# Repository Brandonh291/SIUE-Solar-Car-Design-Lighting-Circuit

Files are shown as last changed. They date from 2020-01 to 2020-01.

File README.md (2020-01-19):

# SIUE-Solar-Car-Design-Lighting-Circuit
Solar Car Lighting Circuit
Lighting Controller MCU specifications

Read through section 9.4 of the 2020 regulations for how the external lights should behave.

Also, download the orion bms wiring sheet, it’ll be useful.

· The lighting controller will dictate when a light on the car turns on and off

· It will control 10 exterior lights

o Two forward facing headlights

o Two forward facing blinkers

o Two lateral blinkers

o Three rear lights, two of which are blinker/break and one of which is a break light

o One BPS trip strobe

· The behavior of the lights is as follows:

o The headlights will be controlled by a toggle switch. When the switch is closed, the headlights will turn on. When the switch is opened the headlights will turn off.

o The blinkers will be controlled by a three-state toggle switch. When the switch is turned left, the forward, lateral, and rear left lights will begin blinking. The same for if the switch is turned right. If the switch is neutral, no blinking will occur.

o The brakes will illuminate when the brake petal is depressed. Two of the three brake lights in the rear of the vehicle will also function as blinkers. When the blinkers and brakes are engaged, the blinkers take priority.

o The hazard will be controlled by a toggle switch. When it is closed, all lights except for the BPS strobe will flash until the switch is opened.

o The BPS strobe is controlled by an open drain output from the Orion BMS. Normal, working conditions will set the output high. When the device detects a battery fault, the output goes low. See the “Digital Signal outputs” section in the Orion BMS wiring manual for more information.

· Power requirements

o Each LED strip burns about 50mA at 12V, so whatever is used to switch them must be capable of handling this load. In the case of the headlights, and each front/lateral set of blinkers, are tied together, so the switch powering them must be able to handle approximately 100mA. There are logic level FETs that can drive the LEDs.

o I want input protection on the switches to make it ESD resistant. A google search for “MCU input protection” will yield plenty of results.

· Hardware and I/O

o It’d be nice if the I/O was confined to a single connector like a D-sub connector or something similar to confine all the connections to a single plug.

Parts List
  * 14 - 3.5mm 2 Pin Screw Terminal Block
  * 7 - 10k Resistors
  * 7 - 2k Resistors
  * 1 - 1M Resistor
  * 1 - Arduino Nano Microcontroller
  * 7 - RFP30N06LE Mosfets
  * 2 - 74HC08N Quad 2 Input AND IC
  * 1 - 74LS04N Hex Inverter IC
  * 1 - 74HC32N Quad 2 Input OR IC
  * 1 - NE555N Timer
  * 1 - 470nF Capacitor
  * 1 - 10nF Capacitor

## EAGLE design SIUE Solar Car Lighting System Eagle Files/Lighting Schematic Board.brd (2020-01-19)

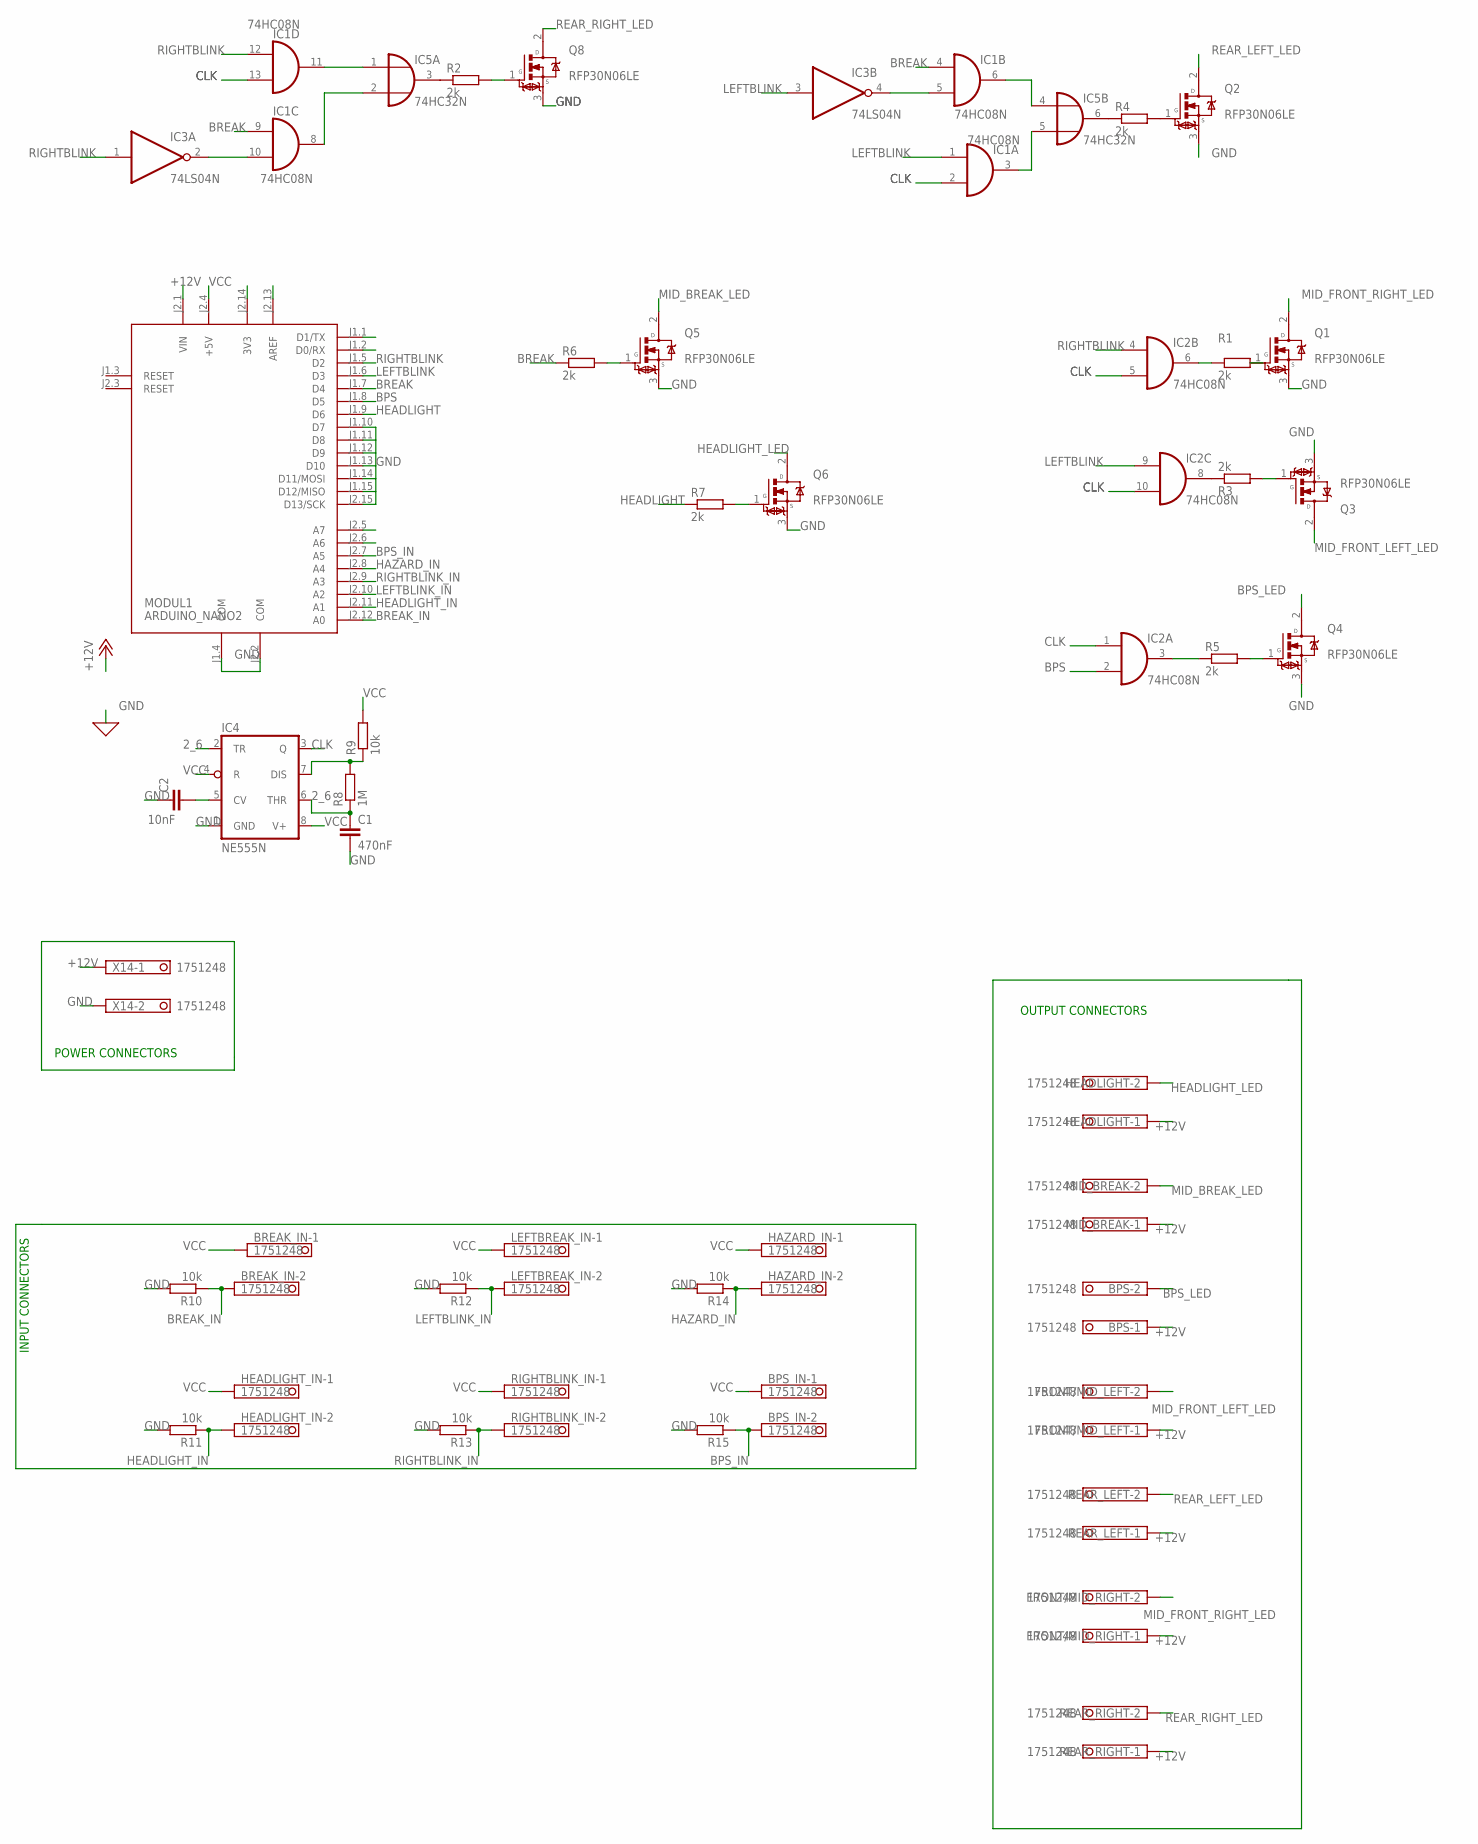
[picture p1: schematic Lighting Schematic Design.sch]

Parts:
BPS: 1751248
BPS_IN: 1751248
BREAK_IN: 1751248
C1: 470nF; C2.5-2
C2: 10nF; C2.5-2
FRONT/MID_LEFT: 1751248
FRONT/MID_RIGHT: 1751248
HAZARD_IN: 1751248
HEADLIGHT: 1751248
HEADLIGHT_IN: 1751248
IC1, IC2: 74HC08N; DIL14
IC3: 74LS04N; DIL14
IC4: NE555N; DIL08
IC5: 74HC32N; DIL14
LEFTBREAK_IN: 1751248
MID_BREAK: 1751248
MODUL1: ARDUINO_NANO2
Q1, Q2, Q3, Q4, Q5, Q6, Q8: RFP30N06LE; TRANS_RFP30N06LE
R1, R2, R3, R4, R5, R6, R7: 2k; 0204/5
R8: 1M; 0204/5
R9, R10, R11, R12, R13, R14, R15: 10k; 0204/5
REAR_LEFT: 1751248
REAR_RIGHT: 1751248
RIGHTBLINK_IN: 1751248
X14: 1751248

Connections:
2_6: C1.1, IC4.2 (TR), IC4.6 (THR), R8.1
+12V: BPS.1, FRONT/MID_LEFT.1, FRONT/MID_RIGHT.1, HEADLIGHT.1, MID_BREAK.1, MODUL1.J2.1 (VIN), REAR_LEFT.1, REAR_RIGHT.1, X14.1
BPS: IC2.2 (I1), MODUL1.J1.8 (D5)
BPS_IN: BPS_IN.2, MODUL1.J2.7 (A5), R15.1
BPS_LED: BPS.2, Q4.2 (D)
BREAK: IC1.4 (I0), IC1.9 (I0), MODUL1.J1.7 (D4), R6.1
BREAK_IN: BREAK_IN.2, MODUL1.J2.12 (A0), R10.1
CLK: IC1.2 (I1), IC1.13 (I1), IC2.1 (I0), IC2.5 (I1), IC2.10 (I1), IC4.3 (Q)
GND: C1.2, C2.1, IC1.7 (GND), IC2.7 (GND), IC3.7 (GND), IC4.1 (GND), IC5.7 (GND), MODUL1.J1.4 (COM), MODUL1.J1.10 (D7), MODUL1.J2.2 (COM), MODUL1.J2.15 (D13/SCK), Q1.3 (S), Q2.3 (S), Q3.3 (S), Q4.3 (S), Q5.3 (S), Q6.3 (S), Q8.3 (S), R10.2, R11.2, R12.2, R13.2, R14.2, R15.2, X14.2
HAZARD_IN: HAZARD_IN.2, MODUL1.J2.8 (A4), R14.1
HEADLIGHT: MODUL1.J1.9 (D6), R7.1
HEADLIGHT_IN: HEADLIGHT_IN.2, MODUL1.J2.11 (A1), R11.1
HEADLIGHT_LED: HEADLIGHT.2, Q6.2 (D)
LEFTBLINK: IC1.1 (I0), IC2.9 (I0), IC3.3 (I), MODUL1.J1.6 (D3)
LEFTBLINK_IN: LEFTBREAK_IN.2, MODUL1.J2.10 (A2), R12.1
MID_BREAK_LED: MID_BREAK.2, Q5.2 (D)
MID_FRONT_LEFT_LED: FRONT/MID_LEFT.2, Q3.2 (D)
MID_FRONT_RIGHT_LED: FRONT/MID_RIGHT.2, Q1.2 (D)
unnamed: Q8.1 (G), R2.2
unnamed: IC1.10 (I1), IC3.2 (O)
unnamed: IC2.6 (O), R1.1
unnamed: IC1.5 (I1), IC3.4 (O)
unnamed: IC4.7 (DIS), R8.2, R9.1
unnamed: Q2.1 (G), R4.2
unnamed: Q1.1 (G), R1.2
unnamed: Q3.1 (G), R3.2
unnamed: Q4.1 (G), R5.2
unnamed: IC2.3 (O), R5.1
unnamed: Q5.1 (G), R6.2
unnamed: Q6.1 (G), R7.2
unnamed: IC2.8 (O), R3.1
unnamed: IC5.3 (O), R2.1
unnamed: IC1.8 (O), IC5.2 (I1)
unnamed: IC1.11 (O), IC5.1 (I0)
unnamed: IC5.6 (O), R4.1
unnamed: IC1.6 (O), IC5.4 (I0)
unnamed: IC1.3 (O), IC5.5 (I1)
unnamed: C2.2, IC4.5 (CV)
REAR_LEFT_LED: Q2.2 (D), REAR_LEFT.2
REAR_RIGHT_LED: Q8.2 (D), REAR_RIGHT.2
RIGHTBLINK: IC1.12 (I0), IC2.4 (I0), IC3.1 (I), MODUL1.J1.5 (D2)
RIGHTBLINK_IN: MODUL1.J2.9 (A3), R13.1, RIGHTBLINK_IN.2
VCC: BPS_IN.1, BREAK_IN.1, HAZARD_IN.1, HEADLIGHT_IN.1, IC1.14 (VCC), IC2.14 (VCC), IC3.14 (VCC), IC4.4 (R), IC4.8 (V+), IC5.14 (VCC), LEFTBREAK_IN.1, MODUL1.J2.4 (+5V), R9.2, RIGHTBLINK_IN.1

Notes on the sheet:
INPUT CONNECTORS
OUTPUT CONNECTORS
POWER CONNECTORS

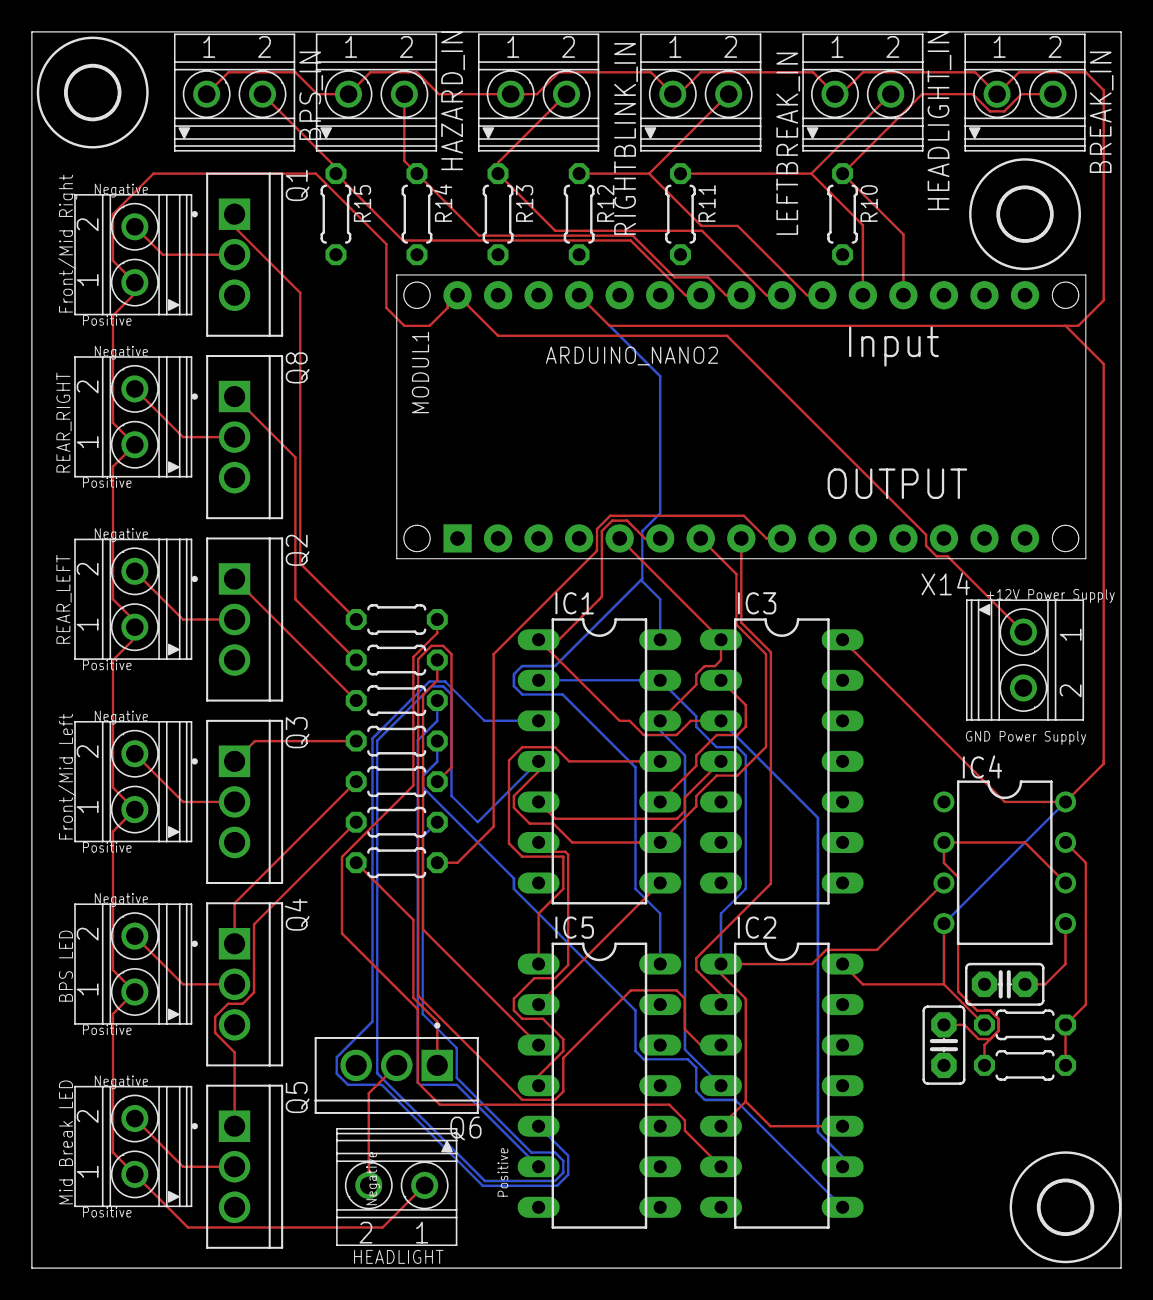
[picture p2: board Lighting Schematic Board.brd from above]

Board: 2 copper layers, 68.2 x 77.5 mm, 47 parts (0 on the bottom side), 43 nets.

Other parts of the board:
U$1, U$2, U$3: 3,2

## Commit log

2020-01-19 Add files via upload
    Several changes made in this version:
    - For the input connections I created an on-board 5V source on the positive end of the Input connector, and then a 10k pull-down resistor connected to the arduino on the other. This should make sure that the arduino isn't reading any floating signals when the switch is open and the 5V can not flow through the switch. The 5V source on the pins will also eliminate the need for an external power supply running across the switches.
    - This 5V source is included on the BPS_IN connector to allow for testing, in practical use since the BMS will be sending an HIGH Output when functioning correctly and go LOW when error is detected we shoul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
    [Lighting Schematic.brd, Lighting Schematic.sch]
2020-01-19 Rename Lighting Schematic.brd to Lighting Schematic Board.brd
    Edit name
    [Lighting Schematic Board.brd]
2020-01-19 Rename Lighting Schematic.sch to Lighting Schematic Design.sch
    [Lighting Schematic Design.sch]
2020-01-19 Delete Lighting Schematic_2020-01-19 CAM Files.zip
    RS-274
